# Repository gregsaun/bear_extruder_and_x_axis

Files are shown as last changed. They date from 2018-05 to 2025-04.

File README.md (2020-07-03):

# Bear Extruder And X Axis (BearExxa)

## Table of contents
  1. [Introduction](#introduction)
  1. [Features](#features)
  1. [Compatibility](#compatibility)
  1. [Printed parts](#printed-parts)
  1. [Print settings](#print-settings)
  1. [Bill of materials](#bill-of-materials)
  1. [Manual](#manual)
  1. [Optional parts](#optional-parts)
  1. [Community](#community)
  1. [Images](#images)
  1. [Source](#source)
  1. [Support my work](#support-my-work)
  1. [Thank you](#thank-you)
  1. [License](#license)
  1. [Credit and inspiration](#credit-and-inspiration)

## Introduction

The BearExxa (Bear extruder and X axis) is an alternative extruder and X axis for Prusa i3 printer and is designed to improve print quality, reliability and ease of maintenance. It is following the [Bear Upgrade project](https://github.com/gregsaun/prusa_i3_bear_upgrade) but also compatible with Original Prusa's MK2(S) and MK3(S) frames.

The Bear X axis also supports alternative extruders such as [Bondtech Prusa Upgrade](./optional_parts/bondtech_x_carriage/README.md), [E3D Hemera](./optional_parts/bear_hemera/README.md) and [vertigo235's extruders](https://www.thingiverse.com/vertigo235/designs).

All parts are available under the GPLv3 open source license. You can download STL, CAD files (Autodesk Fusion 360) or STEP files. Feel free to fork and share!

:warning: The Bear X axis is **NOT** compatible with stock Prusa extruder!

## Features

### Bear X axis (and X carriage)

  * Simple and precise belt tensioning system
  * Stiffer X axis design to reduce ringing
  * Easier Z bearings installation thanks to clamping system
  * Optimized belt path for smoother movements
  * Easy access to belt and extruder cables
  * Improved X axis bearing alignment
  * Kinematic constraint to self-center the X stepper
  * Optional: Support for alternative extruders
  * Optional: Compatible with E3D Gates idlers

### Bear extruder

  * Better heat management to reduce inconsistency, clogs and heatcreap (also check these [recommended hotend fans](optional_parts/hotend_fan/README.md))
  * Stiffer extruder thanks to a uni-body structure
  * Easier installation and removal of E3D v6 hotend
  * Efficient part cooling
  * Self-centering of extruder motor and Bondtech gears
  * Reduced risk of [extruder blob](https://www.prusa3d.com/extruder-blob/)
  * Reliable filament sensor (based on MK2.5S/MK3S sensor)
  * Perfectly aligned filament path
  * Reduced extruder and Bondtech gear vibrations
  * Reduced wear and noise of print fan thanks to a vertical assembly
  * Optional: Compatible with MMU2S thanks to the work of [vertigo235](https://www.thingiverse.com/vertigo235/designs)

### Alternative extruders (optional)

The Bear X axis is also compatible with several alternative extruders. See [optional parts](#optional-parts) to get all the information and files for those alternative extruders.

  * [E3D Hemera](optional_parts/bear_hemera/README.md)
  * [Bondtech Prusa Upgrade extruder](optional_parts/bondtech_x_carriage/README.md)
  * [Bear extruder for MMU2S by vertigo235](https://www.thingiverse.com/thing:3472911)
  * [Gear box for Bear extruder by vertigo235](https://www.thingiverse.com/thing:3714978)
  * [Bear Extruder BLTouch Mount by vertigo235](https://www.thingiverse.com/thing:3251530)

## Compatibility

Due to a different belt path, the Bear X axis and extruders are matched to each other __and cannot be used separately__. As a unit, they are compatible with both Original Prusa frames and Bear Upgrade frames.

  * The Bear extruder version supports the new IR filament sensor introduced with the latest Original Prusa MK2.5S/MK3S extruder.
  * The Bear extruder version is compatible with original Prusa firmware for daily use. However, (XY)Z calibration and selftest require a dedicated firmware for these steps only.
  * MK2.5 (non-S) and MK3 (non-S) are compatible with this Bear extruder version with the exception of the filament sensor.

In an effort to lengthen the Z axis, the original Prusa MK2.5S/MK3S hotend was raised by [about 6mm](doc/prusa_mk3_mk3s_size_diff_01.jpg). This placement increases the ambient temperature around heatbreak and heatblock which could lead to print quality and reliability issues. We have decided to not lengthen the Z axis in order to provide best printing experience. Because of this difference with the original Prusa extruder, we provide a customized firmware to pass Selftest and (XY)Z Calibration. Except for these steps, the original Prusa firmware is completely compatible with our extruder.

The firmware is available here: https://github.com/bear-lab-3d/Prusa-Firmware/releases/

## Printed parts

Download links for the Bear extruder and X axis (BearExxa) :
* BearExxa MK2.5S : [bear_extruder_x_axis_mk2.5s.zip](printed_parts/bear_extruder_x_axis_mk2.5s.zip?raw=true)
* BearExxa MK3S : [bear_extruder_x_axis_mk3s.zip](printed_parts/bear_extruder_x_axis_mk3s.zip?raw=true)
* Sources : [bear_extruder_x_axis_source.zip](source/bear_extruder_x_axis_source.zip?raw=true)

You can also download them via Thingiverse: [thingiverse.com/thing:4362586](https://www.thingiverse.com/thing:4362586)

If you are looking for alternative extruders printed parts, please check the section [Optional parts](#optional-parts) below.

## Print Settings

The parts have been designed and tested with the parameters below and it is important to follow them to avoid issues like part cracking, bad bridging, not enough stiffness or wrong tolerances.

[Read the print settings here](manual/print_settings.md).

## Bill of materials

[Read the BOM here](manual/bom.md).

## Manual

The manual contains bill of materials (BOM), print settings and assembly instructions.

[Read the manual on guides.bear-lab.com :book:](https://guides.bear-lab.com/c/95jghwzvw9l46s3g)

## Optional parts

Here is a list of optional parts designed for the Bear extruder and X axis (BearExxa).

| Description | Link |
|---|---|
| E3D Hemera mount (BearMera) | [bear_hemera](optional_parts/bear_hemera/README.md) |
| X carriage for Bondtech extruder | [bondtech_x_carriage](optional_parts/bondtech_x_carriage/README.md) |
| Hotend fan (Sunon / Delta) | [hotend_fan](optional_parts/hotend_fan/README.md) |
| X end tensioner for E3D idlers | [x_end_idler_tensioner_e3d](optional_parts/x_end_idler_tensioner_e3d/README.md) |
| Reverse bowden adapters | [reverse_bowden](optional_parts/reverse_bowden/README.md) |
| X carriage back for larger filament sensor cable |[x_carriage_back_larger_cable](optional_parts/x_carriage_back_larger_cable/README.md) |

You can also find optional parts made by the community at [guides.bear-lab.com/Wiki/community_optional_parts](https://guides.bear-lab.com/Wiki/community_optional_parts).

## Community

Here are the places were the Bear project is the most active. Do not hesitate to ask if you have a question :

* Facebook group : [facebook.com/groups/PrusaBearUpgrade](https://www.facebook.com/groups/PrusaBearUpgrade)
* Discord server of "The 602 Wasteland" community : [discordapp.com/invite/hYUjSnW](https://discordapp.com/invite/hYUjSnW)
* Twitter : [@gregoiresaunier](https://twitter.com/gregoiresaunier)
* GitHub : [github.com/gregsaun](https://github.com/gregsaun)

## Images

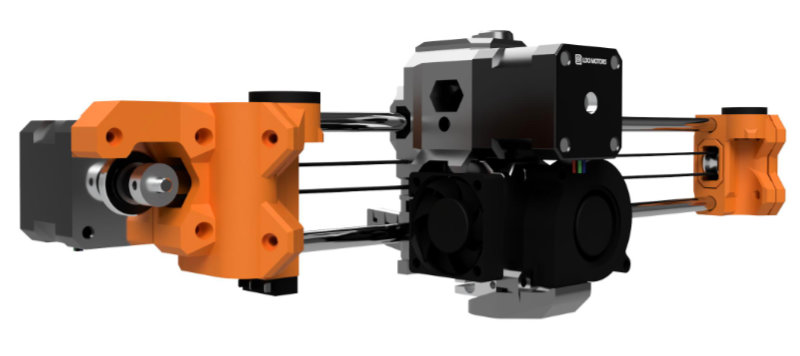
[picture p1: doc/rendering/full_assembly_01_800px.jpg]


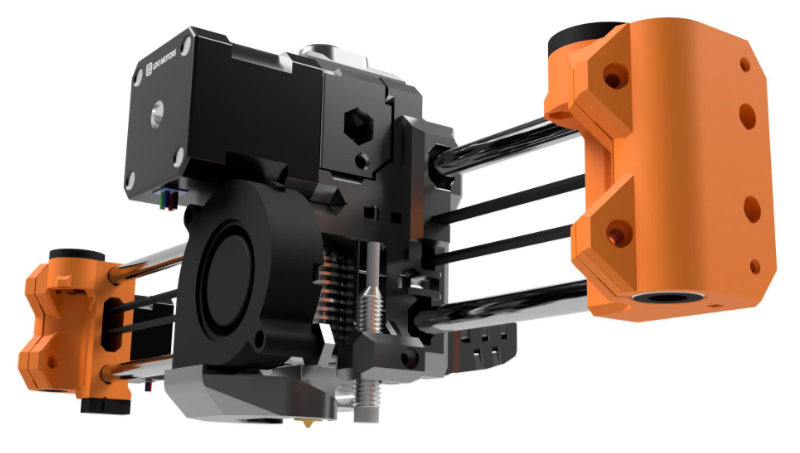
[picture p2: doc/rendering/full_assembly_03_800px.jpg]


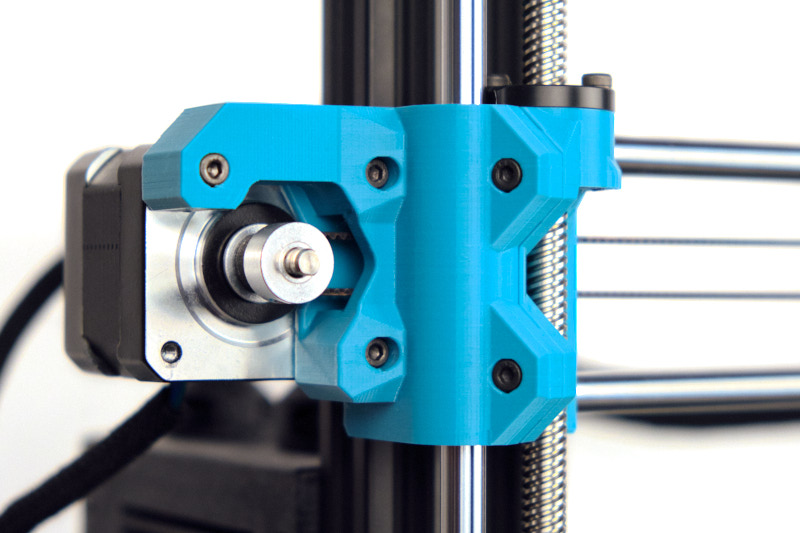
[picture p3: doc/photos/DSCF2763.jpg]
Bear X end motor


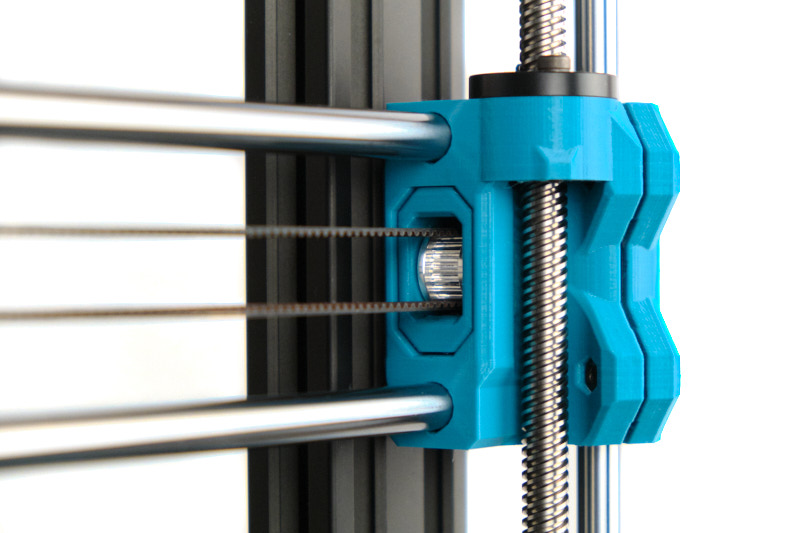
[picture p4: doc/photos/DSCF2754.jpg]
Bear X end idler


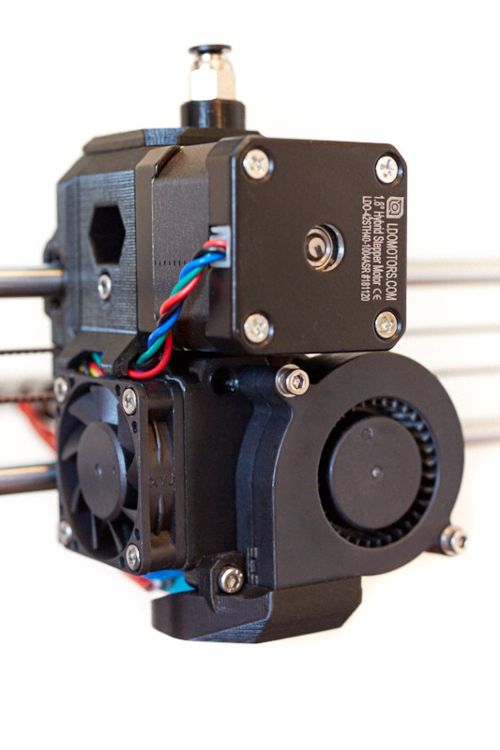
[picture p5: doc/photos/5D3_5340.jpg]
Bear extruder


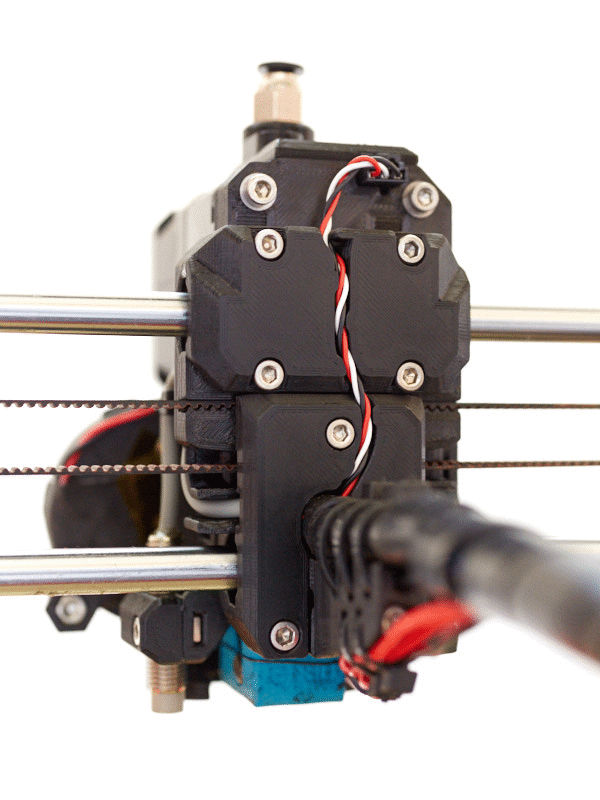
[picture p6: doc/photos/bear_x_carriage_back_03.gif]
Bear extruder X carriage back


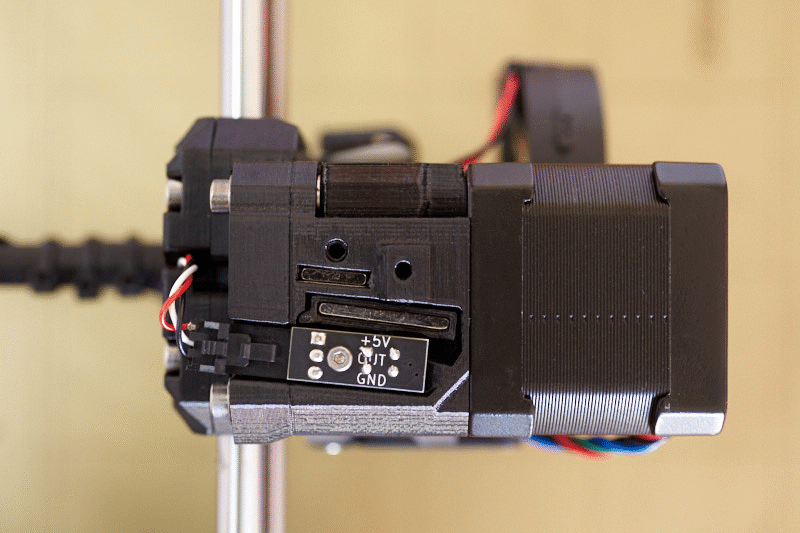
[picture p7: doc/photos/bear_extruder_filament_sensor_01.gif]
Bear extruder filament sensor


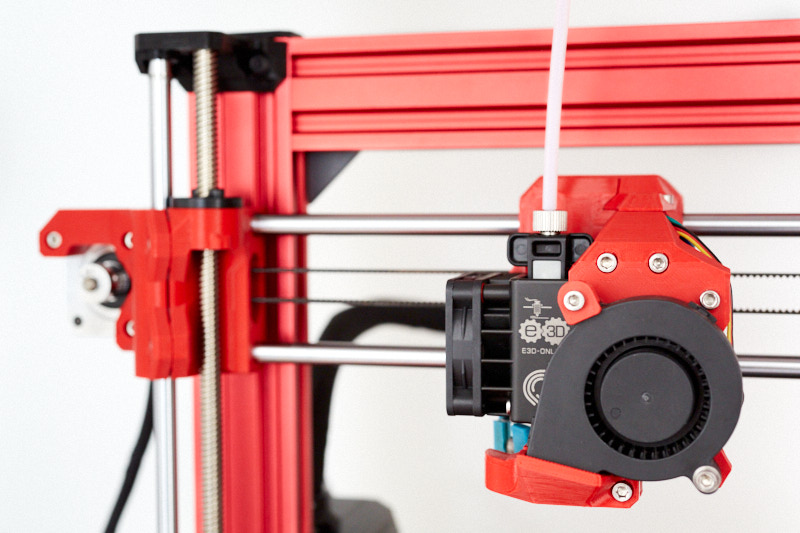
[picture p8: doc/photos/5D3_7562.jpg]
Bear E3D Hemera


> Pictures from Flobler and Grégoire Saunier

## Source

All source files in Fusion 360 and STEP format can be [download here](source/bear_extruder_x_axis_source.zip?raw=true).

## Support my work

The Bear project is only possible thanks its supporters, you can participate via
<br/><br/>
become a patron (https://www.patreon.com/gregsaun)<br/>[patreon.com/gregsaun](https://www.patreon.com/gregsaun)
<br/><br/>
paypal.me (https://www.paypal.me/gregsaun)<br/>[paypal.me/gregsaun](https://www.paypal.me/gregsaun)
<br/><br/>
 You can also send me a tip via [Thingiverse](https://www.thingiverse.com/pekcitron/about) if you prefer.

Massive thank you in advance :heart:

## Thank you

First of all, massive thank you to [Adrian Bowyer](https://github.com/AdrianBowyer/) for having invented [RepRap](http://reprapltd.com).

Thank you to all [my Patreon's](https://guides.bear-lab.com/Wiki/Bear_Supporters)

Thank you to David Ogles, Flobler, Jason from LDO Motors, Matthew Humphrey, Nathan Denkin, Orlando from All3DMakers, Saiz, Sleene, Termlimit, Vertigo235 for helping me in developing the Bear project.

Thank you to all that have sent me a tip on Thingiverse and PayPal.

Thank you to everybody from Facebook group and The 602 Wasteland community.

Thank you for having purchased a kit from an official distributor.

Thank you to all official distributors for taking care of the kits and customers.

Thank you Jason from LDO Motors for the quality manufacturing and relationship.

Thank you Openbuilds for your hardware, community and state of mind.

Thank you for making the community alive with all your comments, issues, pull requests, optional parts, make, pictures, etc.

## License

This repository and all its files are licensed under the GPLv3 license. Here is a quick summary; for more details please check the LICENSE file.

What you __can__ do:
  * Modify
  * Distribute
  * Private, commercial and patent use

What you __must__ do:
  * Include copyright notice
  * Include a copy of the license
  * Share source files
  * Use the same license (GPLv3)
  * Document changes applied

## Credit and inspiration

* RepRap : https://reprap.org
* Prusa : http://www.prusa3d.com
* Vecko Kojchevski for the help on some details of the X end clamps, X carriage and PTFE cutter : https://www.thingiverse.com/vekoj/designs
* Arnaud Rousseau for "his X-Ends clamped MK3 (Zaribo)" : https://www.thingiverse.com/thing:2964026
* Prusa i3 Solidworks parts from jzkmath : https://github.com/jzkmath/Original-Prusa-i3
* Prusa MK2/S X-Carriage Adjustable Tensioner by Jon Madden : https://www.thingiverse.com/thing:2770019
* Jan Imrich from [Kurzy Kocour](https://www.facebook.com/KurzyKocour/) maker space for all his hard work on inconsistency issue
* The 602 Wasteland Discord community for their precious knowledge and advice
* [RH_Dreambox](https://www.thingiverse.com/RH_Dreambox/about) and [Robrps](https://www.thingiverse.com/robrps/designs) for his nozzle fan duct designs
* Joel from [Bondtech](https://www.bondtech.se/en/product/prusa-i3-mk2-5-mk3-extruder-upgrade/) for having pushed me to pursue the filament sensor idea

Massive thanks to these projects, without them this project cannot exist!

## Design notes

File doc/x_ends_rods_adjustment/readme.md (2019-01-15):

This explains how to adjust the rod tensioning screws on the x end idler. It also discusses the limits of Prusa’s X axis design.

Those screws were present on the MK2s but were removed on the MK3, perhaps making it simpler for the user and to reduce cost. However, while not obvious, those screws can play a critical role.

Due to manufacturing tolerances, user assembly and somewhat flexible printed parts (especially PETG), the X axis length between the Z axis smooth rods will differ between assemblies, for both Bear and original Prusa printers.

This first picture shows an exaggerated view of what is happening when tensioning the belt with too short X smooth rods.

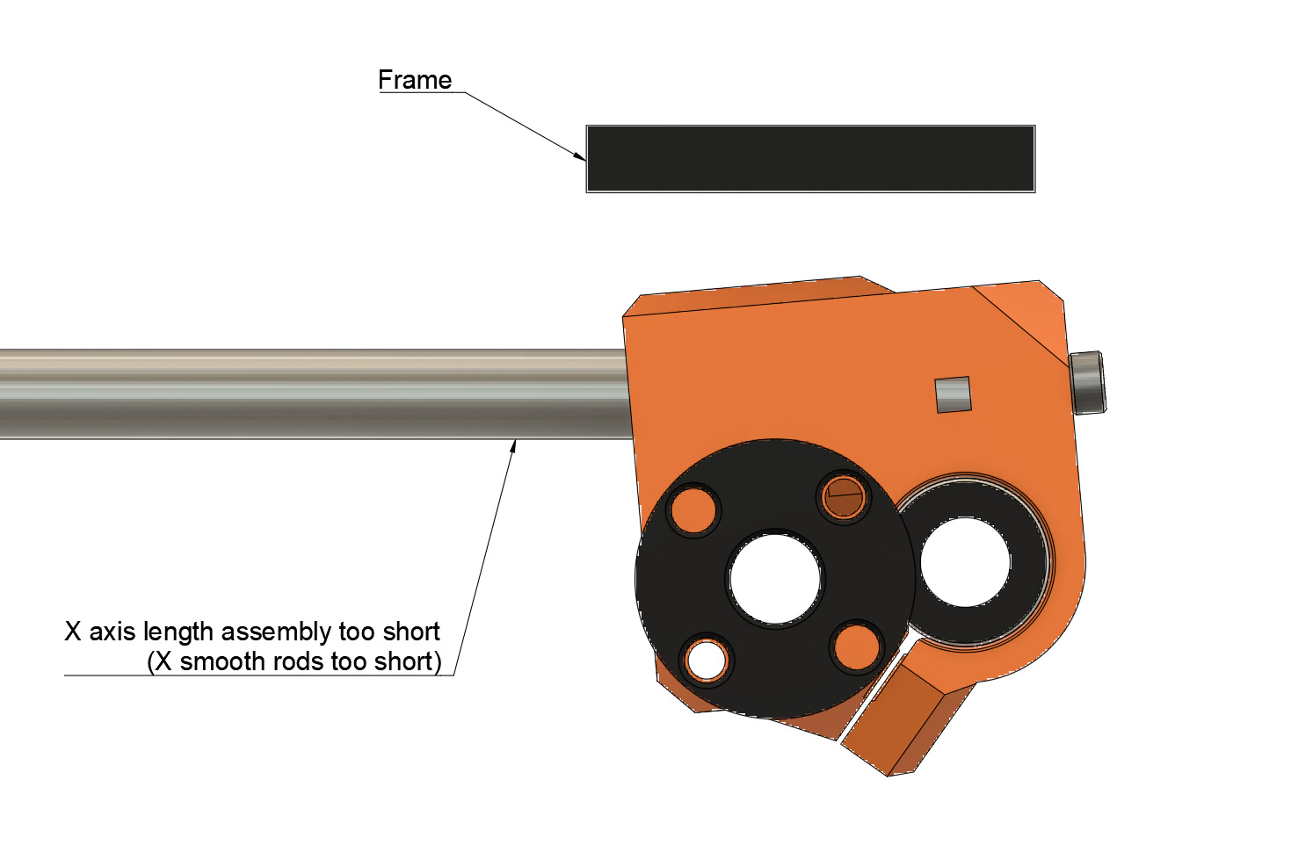
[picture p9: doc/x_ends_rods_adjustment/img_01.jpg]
X axis length too short


This second picture shows when the X smooth rods are too long.

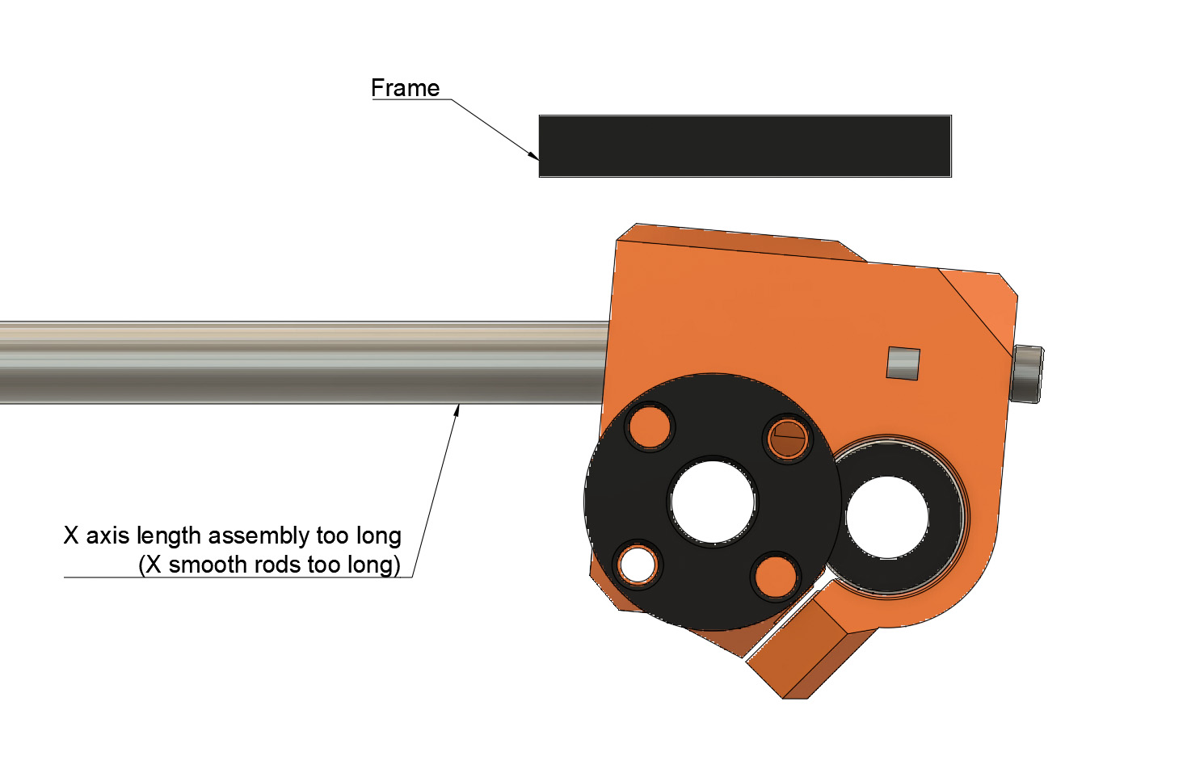
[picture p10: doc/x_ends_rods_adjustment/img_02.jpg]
X axis length too long


These rotations of the X end idler around the Z axis result because the ends X smooth rods are not aligned with the Z axis generating a torque that twists the X end idler. The rod tensioning screws can be used to reduce that torque. 

The third picute shows when the tensioning screw are correctly set, the X end idler is parallel to the frame

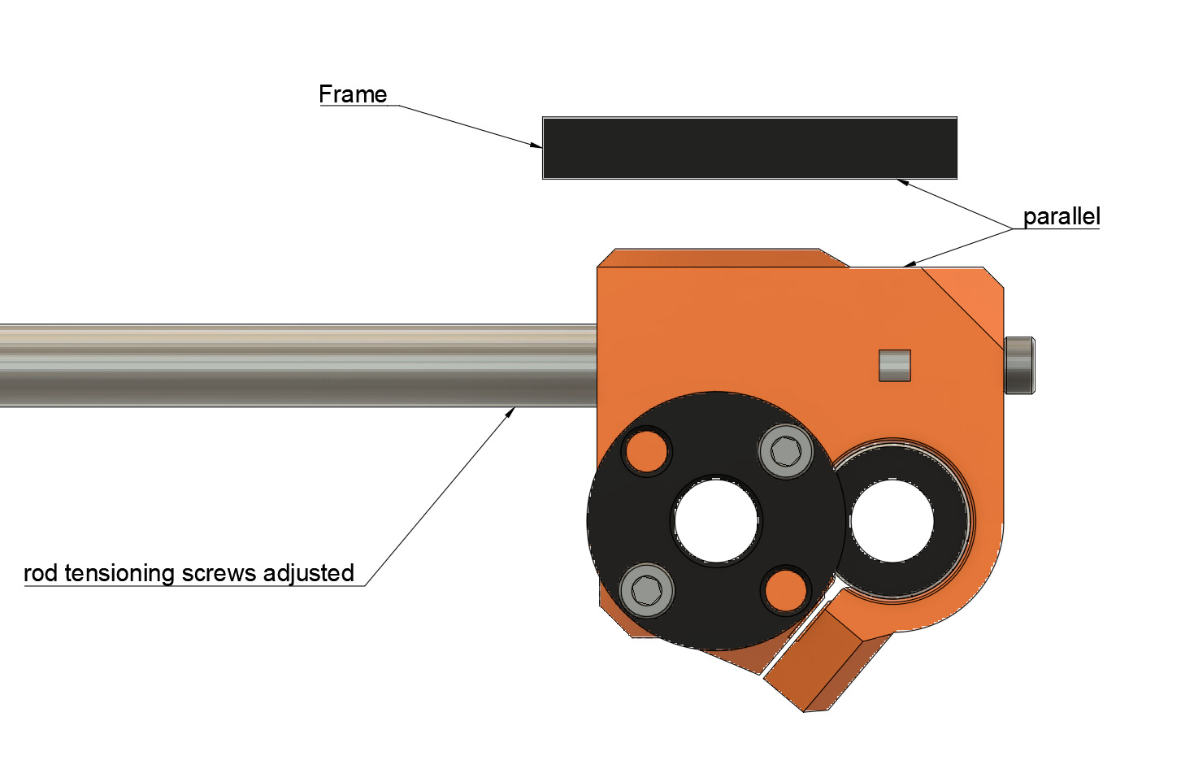
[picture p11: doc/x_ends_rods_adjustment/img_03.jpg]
X axis length good


A good way to check if the X end idler is parallel is to use a machinist square like it this picture.

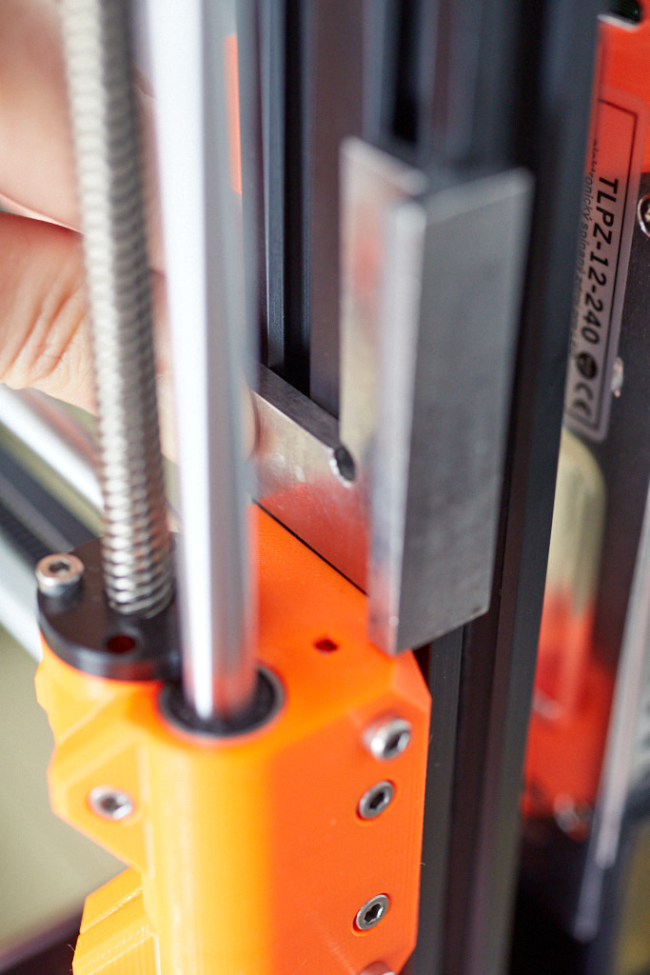
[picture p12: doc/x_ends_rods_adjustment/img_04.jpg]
X axis check


Usually, the pairs of smooth rods have the same length; in that case, both rod tensioning screw heads should stick out of the X end idler by the same distance that could be verified by a caliper.

However, with Prusa’s design, the X axis and Z axis interact. If the distance between the X end idler and the X motor is too large, the Z rods would be pushed apart, and you would see that the Z rods off-center in with respect to the Z tops. Similarly, if the distance between the X end idler and the X motor is too small, the Z rods would be pulled together. The trapezoidal lead screw nut has some play and can influence this. The screws securing both trapezoidal nuts should be loosened while the X axis is being adjusted. All these interactions makes a perfect assembly almost impossible to achieve.

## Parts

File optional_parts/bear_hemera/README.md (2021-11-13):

# Bear X axis and Extruder

## BearMera for E3D Hemera extruder

### Table of contents
  1. [Introduction](#introduction)
  1. [Compatibility](#compatibility)
  1. [Bill Of materials](#bill-of-materials)
  1. [Printed parts](#printed-parts)
  1. [Print settings](#print-settings)
  1. [Assembly guide](#assembly-guide)
  1. [Optional parts](#optional-parts)
  1. [Source](#source)
  1. [Thank you](#thank-you)
  1. [Credit and inspiration](#credit-and-inspiration)

### Introduction

This page contains all the files and information to use the Bear X axis with the original [E3D Hemera](https://e3d-online.com/e3d-hemera).

The Hemera needs a dedicated mount to be used with the Bear X axis. All hardware and printed parts needed are available in the [Bill of Materials](#bill-of-materials) section below.

Note: The BearMera reduces a little the print surface to 205x240mm (compared to 210x250mm for Original Prusa).

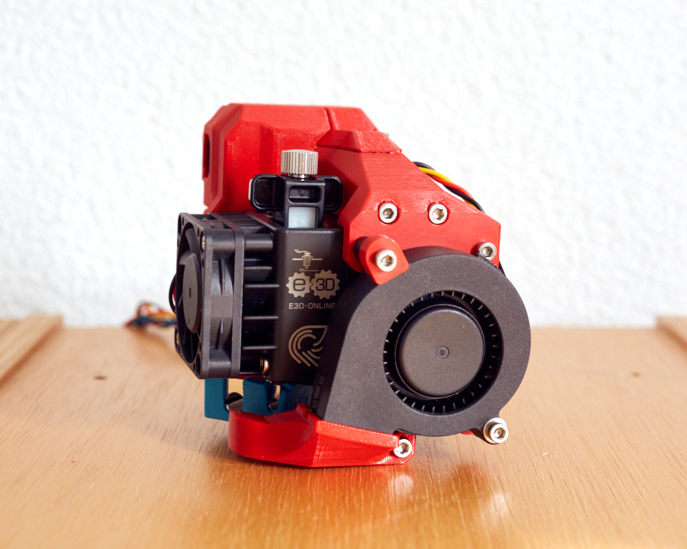
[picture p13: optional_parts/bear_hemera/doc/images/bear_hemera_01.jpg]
Bear Hemera body


### Compatibility

The BearMera has a smaller print surface compared to the Original Prusa, Bear and Bondtech extruders: 205x240mm for BearMera, 210x250mm for Bear extruder.

The BearMera is compatible with Original Prusa as well as Bear frame. You must use the Bear X axis in both cases.

This BearMera is only compatible with the Bear X axis.

This BearMera is **NOT** compatible with the original Prusa X axis.

You will need to replace **all** printed parts if you are already using the Bear X axis (with another extruder) of version **equal or smaller than 0.7.0-beta**.

### Bill Of materials

#### Hardware BOM for Original Prusa printers

This is the list of extra material you will need from original Prusa extruder and X axis.

| Part | Quantity<br>(pce) | Detail | Example Link |
|---|:---:|---|---|
| E3D Hemera Direct Kit | 1 | 24V for MK3(S)(S+)<br>12V for MK2(S) and MK2.5(S)(S+) | [E3D-Online store](https://e3d-online.com/e3d-hemera) |
| Hotend fan | 1 | Stock Hemera fan<br/>or higher specifications (yet unknown) | |
| M3x8mm socket head screw (ISO 4762) | 3 | Check your Hemera package | [McMaster-Carr](https://www.mcmaster.com/90751a111) | |
| M3x10mm socket head screw (ISO 4762) | 12 | | [McMaster-Carr](https://www.mcmaster.com/#91292a113/=1coixe5) | |
| M3x18mm socket head screw (ISO 4762) | 16 | | [McMaster-Carr](https://www.mcmaster.com/#91292a029/=1coixwt) | |
| M3x25mm socket head screw (ISO 4762) | 2  | | [McMaster-Carr](https://www.mcmaster.com/#91292a020/=1cok8ux) | |
| M3x40mm socket head screw (ISO 4762) | 3  | | [McMaster-Carr](https://www.mcmaster.com/#91292a024/=1coj8pe) | |
| M2x12mm socket head screw (ISO 4762) | 2  | :warning: MK2(S) or MK2.5(S) only | [McMaster-Carr](https://www.mcmaster.com/#91292a834/=1cok8m8) |
| M3 Hex nylock nuts (DIN 985) | 3  | | |
| M3 Hex nuts (DIN 934) | 15 | | |
| M3 Square nuts (DIN 562) | 6  | 1.8mm thick and 5.5mm wide | |
| M3 Steel washer (DIN 125), 0.5mm thick | 1  | | |
| Zip ties 2.5x100mm | 5  | | |
| Dowel pin<br/>diameter: 3mm, length: 15mm to 15.8mm | 1 | Must fit the 2GT idler bearing.<br/>:pushpin: Cut a M3 screw if you can't find one |

#### Additional BOM for scratch build

| Part | Quantity<br>(pce) | Detail | Example Link |
|---|:---:|---|---|
| Nema 17 stepper for X axis<br/>LDO 42STH38-1004A100CM | 1 | [Datasheet](https://github.com/gregsaun/bear_extruder_and_x_axis/tree/master/doc/datasheets/LDO-42STH38-1004A100CM-RevA-for-3D.pdf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) | [Prusa](https://shop.prusa3d.com/en/mk3mk3s/388-x-axis-stepper-motor.html) |
| Nema 17 stepper for Z axis<br/>integrated Lead screw Tr8x8 (P2x4) and nut<br/>LDO-42STH34-1004L321E100CM | 2 | [Datasheet](https://github.com/gregsaun/bear_extruder_and_x_axis/tree/master/doc/datasheets/LDO-42STH34-1004L321E100CM-RevA-for-3D.pdf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) | [Prusa](https://shop.prusa3d.com/en/spare-parts/386-stepper-motor-z-axis-right.html) |
| Nozzle Fan | 1 | Minimal specifications:<br/>- CFM: 3.8<br/>- Static Pressure: 11.3 mmH2O<br/>- Bearing type: ball bearing | [Prusa](https://shop.prusa3d.com/en/spare-parts/201-print-fan.html) |
| Inductive Sensor | 1 | Diameter of 8mm, length around 35mm | | [Prusa](https://shop.prusa3d.com/en/spare-parts/200-pinda-probe-v2.html) |
| Filament sensor<br/>with magnets, steel ball and cables | 1 | 1x IR Sensor: [GitHub Prusa](https://github.com/prusa3d/MKxS-IR-sensor)<br/>1x Steel ball 7mm diameter<br/>1x Magnet 20x6x2<br/>1x Magnet 10x6x2<br/> | [Prusa](https://shop.prusa3d.com/en/upgrades/898-original-prusa-i3-mk3-to-mk3s-upgrade-kit.html#) |
| 2GT 16T pulley | 1 | 3mm bore<br/> | [E3D-Online store](https://e3d-online.com/gates-powergrip-pulley-16-tooth-6mm) |
| 2GT 20T idler | 1 | 3mm bore<br/>smooth or toothed<br/>Check this [optional part for E3D idler](https://github.com/gregsaun/bear_extruder_and_x_axis/tree/master/optional_parts/x_end_idler_tensioner_e3d) | |
| Smooth rods | 2 | 8mm diameter H6<br/>370mm long | [Prusa](https://shop.prusa3d.com/en/mk3mk3s/589-smooth-rod-8x370-x-axis-1-piece.html) |
| LM8UU bearings | 3 | [Prusa](https://shop.prusa3d.com/en/mk3mk3s/140-linear-bearing-lm8uu.html) |
| Gates LL-2GT RF belt | 1 | 6mm width<br/>880mm long | [E3D-Online store](https://e3d-online.com/gates-powergripr-gt2-belt-6mm-x-100mm) |
| Nylon cable<br/>2.85-3.00mm diameter<br/>500mm long | 1 | You can use 2.85mm sample or cleaning filaments | |

### Printed parts

Download links for the BearMera and X axis:
  * BearMera and X axis for MK2(S) and MK2.5(S): [bearmera_mk2_mk2s_mk2.5_mk2.5s.zip](printed_parts/bearmera_mk2_mk2s_mk2.5_mk2.5s.zip?raw=true)
  * BearMera and X axis for MK3(S) and MK3(S): [bearmera_mk3_mk3s.zip](printed_parts/bearmera_mk3_mk3s.zip?raw=true)

### Print settings

:warning: Warning: The parts have been designed and tested with the parameters below and it is important to follow them to avoid issues like part cracking, bad bridging, not enough stiffness or wrong tolerances. Be sure to have a well calibrated machine and extruder. Check our guide here for [calibrating extrusion multiplier](https://guides.bear-lab.com/Guide/Extrusion+multiplier+and+filament+diameter/8?lang=en)

  * Slicer : PrusaSlicer recommended
  * Infill type : Gyroid recommended
  * Support : No
  * Brim : No
  * Detect thin walls : No
  * Perimeters width (internal and external) : 0.45mm

| Part | Quantity | Layer Height | Infill | Perimeters | Top/Bottom Layers | Filament Type |
|:----|:----:|:----:|:----:|:----:|:----:|:----:|
| body_back | 1 | 0.20mm | 20% | 4 | 5 | PETG |
| body_front<sup>1</sup>  | 1 | 0.20mm | 20% | 4 | 5 | PETG |
| cable_cover | 1 | 0.20mm | 20% | 4 | 5 | PETG |
| nozzle_fan_duct | 1 | 0.20mm | 20% | 3 | 5 | Read note<sup>2</sup> below |
| nozzle_fan_spacer | 1 | 0.20mm | 20% | 4 | 5 | PETG |
| pinda_mount | 1 | 0.20mm | 20% | 4 | 5 | PETG |
| ptfe_collet_clip | 1 | 0.20mm | 20% | 3 | 5 | PETG |
| y_axis_end_stop | 1 | 0.20mm | 20% | 3 | 5 | PETG |
| x_carriage | 1 | 0.20mm | 20% | 4 | 5 | PETG |
| x_carriage_back | 1 | 0.20mm | 20% | 3 | 5 | PETG |
| x_end_idler | 1 | 0.20mm | 20% | 4 | 5 | PETG |
| x_end_idler_tensioner | 1 | 0.20mm | 20% | 4 | 5 | PETG |
| x_end_motor | 1 | 0.20mm | 20% | 4 | 5 | PETG |
| cable_guide_back_a | 1 | 0.20mm | 20% | 4 | 5 | PETG |
| cable_guide_back_b | 1 | 0.20mm | 20% | 4 | 5 | PETG |

Note<sup>1</sup>: If you intend to use the E3D Volcano hotend with BearMera, this STL should be replaced with the [modified volcano body_front](optional_parts/e3d_volcano/) listed below among official [Optional parts](#optional-parts)

Note<sup>2</sup>: The nozzle_fan_duct needs to be printed with a heat resistant filament like ABS, Extrudr GreenTec Pro, annealed HTPLA, PC and probably much more. Don't forget to compensate for shrinkage accordingly to the filament type you are using.

You can find more details about recommended filaments in on our [FAQ](https://guides.bear-lab.com/Wiki/Bear_FAQ).

### Assembly guide

The assembly guide is available on [guides.bear-lab.com](https://guides.bear-lab.com/c/r63d85yfkvrohzf1).

### Optional parts

Here is a list official optional parts for your BearMera.

| Name | Description | Link |
|---|---|---|
| E3D Volcano | A body_front to support E3D Volcano | [optional_parts/e3d_volcano](optional_parts/e3d_volcano/) |
| Fan washer | Allow a stronger tightening of the E3D fan by avoiding it to twist | [optional_parts/fan_washer](optional_parts/fan_washer/) |

### Source

All source files in Fusion 360 and STEP format can be [download here](source/bearmera_source.zip?raw=true).

### Thank you

Thank you to [E3D-Online](https://e3d-online.com) for their warm encouragement and for having sponsor this development with a free Hemera.

### Credit and inspiration

  * E3D Hemera Prusa i3 MK2(S) upgrade: https://e3d-online.dozuki.com/Guide/Hemera+Prusa+i3+MK2-2s+upgrade/138?lang=en

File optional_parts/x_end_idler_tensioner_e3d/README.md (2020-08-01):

# Bear X axis and Extruder (BearExxa)

## X-End Idler Tensioner for E3D toothed idler

### Introduction

This is a X end idler tensioner compatible with E3D toothed idler.

### Bill of materials

This is the list of extra material you will need from original Prusa extruder

| Part | Quantity<br>(pce) | Detail |
|---|:---:|---|
| Bear X axis | 1 | From version 0.6.0-a and greater |
| E3D Gates 2GT Toothed Idler<br/>6mm Belt, 20 Tooth, 5mm ID | 1 | https://e3d-online.com/products/gates-powergrip%C2%AE-2gt-idlers |
| Dowel pin<br/>diameter: 4.90-4.95mm<br/>length: 15mm-15.8mm | 1 | Must fit the 2GT idler bearing.<br/>:pushpin: Cut a M5 screw if you can't find one |
| M3 Hex nylock nuts (DIN 985) | 2 | Same as original Bear X end idler tensioner |

### Printed parts

Use this link to download the STL: [x_end_idler_tensioner_e3d.stl](printed_parts/x_end_idler_tensioner_e3d.stl?raw=true)

### Print settings

:warning: Warning: The parts have been designed and tested with the parameters below and it is important to follow them to avoid issues like part cracking, bad bridging, not enough stiffness or wrong tolerances. Be sure to have a well calibrated machine and extruder. Check our guide here for [calibrating extrusion multiplier](https://guides.bear-lab.com/Guide/Extrusion+multiplier+and+filament+diameter/8?lang=en)

  * Slicer : PrusaSlicer recommended
  * Infill type : Gyroid recommended
  * Support : No
  * Brim : No
  * Detect thin walls : No
  * Perimeters width (internal and external) : 0.45mm

| Layer Height | Infill | Perimeters | Top/Bottom Layers |
|:----:|:----:|:----:|:----:|
| 0.20mm | 20% | 4 | 5 |

### Credits

Thanks to Matthew Humphrey for having created the first version of this idler.
https://www.thingiverse.com/thing:3308226

What is changing from Matthew's design:
  * Improves shape and tolerances around the E3D idler
  * Derivation from the original design (using F360 derive feature)

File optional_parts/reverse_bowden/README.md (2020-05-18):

# Bear X axis and Extruder (BearExxa)

## Reverse Bowden

### Introduction

Reverse bowden has the advantage to reduce vibration and tension from the spool holder. It is also useful to guide the filament if the spool holder is not on top of the frame.

The filament sensor cover can be used alone for MMU2.

The vslot mount is available in two versions: angled or normal.

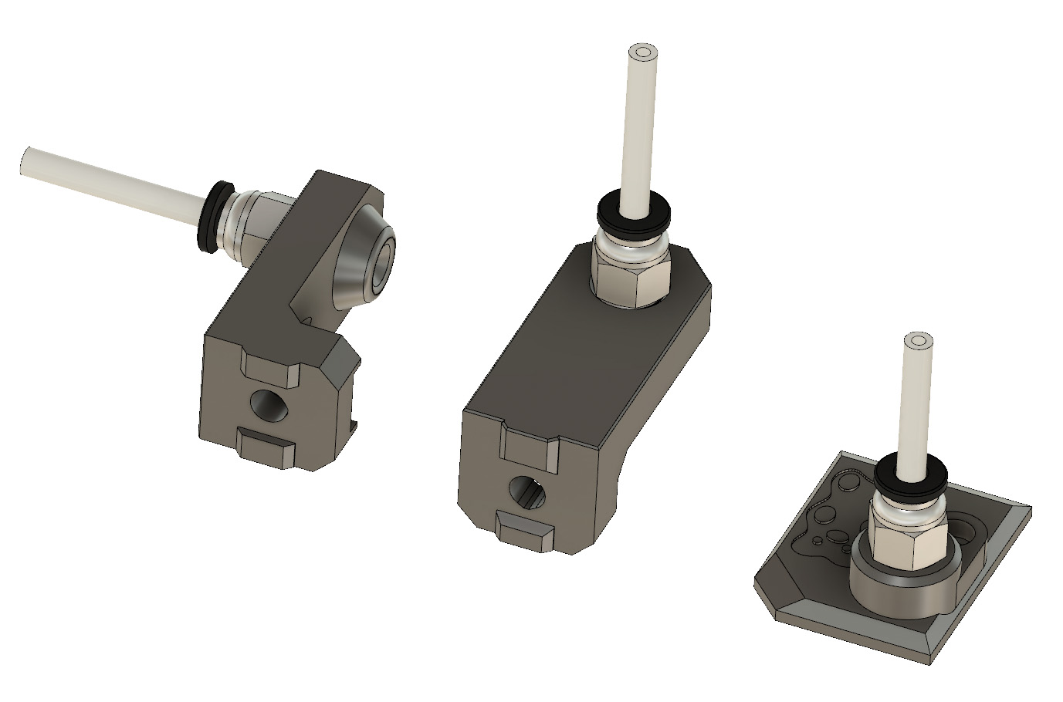
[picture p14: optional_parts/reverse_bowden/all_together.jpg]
Reverse bowden family


### Bill of Materials

| Part | Number<br>(pce) | Detail |
|---|:---:|---|
| Bear extruder and x axis| 1 | |
| PC4-M10 fitting | 2 | |
| PTFE tube | 1 | ID: 2mm, OD: 4mm |
| M5x10 screw | 1 | |

### Printed parts

Use those links to download the STL files:
  * [fs_cover_pc4-m10_mk25s_mk3s.stl](printed_parts/fs_cover_pc4-m10_mk25s_mk3s.stl?raw=true)
  * [vslot_mount_pc4-m10.stl](printed_parts/vslot_mount_pc4-m10.stl?raw=true)
  * [vslot_mount_pc4-m10_angled.stl](printed_parts/vslot_mount_pc4-m10_angled.stl?raw=true)

### Printed Settings

:warning: Warning: The parts have been designed and tested with the parameters below and it is important to follow them to avoid issues like part cracking, bad bridging, not enough stiffness or wrong tolerances. Be sure to have a well calibrated machine and extruder. Check our guide here for [calibrating extrusion multiplier](https://guides.bear-lab.com/Guide/Extrusion+multiplier+and+filament+diameter/8?lang=en)

  * Slicer : PrusaSlicer recommended
  * Infill type : Gyroid recommended
  * Support : No
  * Brim : No
  * Detect thin walls : No
  * Perimeters width (internal and external) : 0.45mm

| Part | Quantity | Layer Height | Infill | Perimeters | Top/Bottom Layers |
|:----|:----:|:----:|:----:|:----:|:----:|
| filament_sensor_cover_pc4-m10 | 1 | 0.20mm | 20% | 3 | 5 |
| vslot_mount_pc4-m10 | 1 | 0.20mm | 20% | 3 | 5 |
| vslot_mount_pc4-m10_angled | 1 | 0.20mm | 20% | 3 | 5 |

### Assembly

1. You need to replace the filament sensor cover by the one included here
1. Attach the vslot mount of your choice to the frame
1. Add the two PC4-M10 fittings
1. Cut the PTFE at the correct length
1. Insert the PTFE tube inside both PC4-M10 (be sure that the PTFE is fully inserted inside the vslot mount)

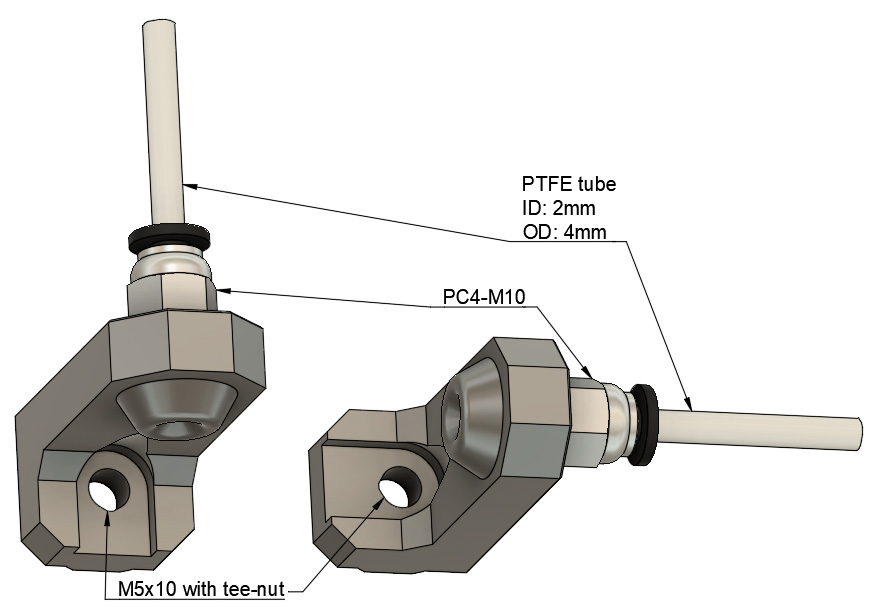
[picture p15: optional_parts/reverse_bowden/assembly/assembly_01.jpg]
Reverse bowden assembly


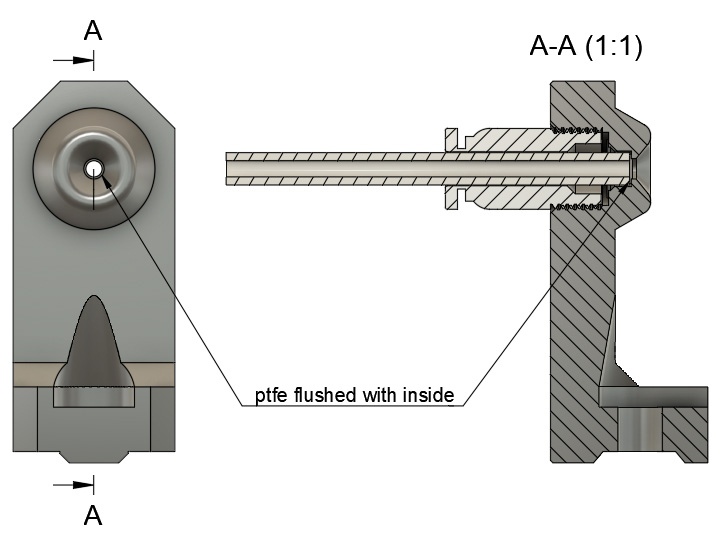
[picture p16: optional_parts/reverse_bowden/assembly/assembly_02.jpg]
Reverse bowden assembly


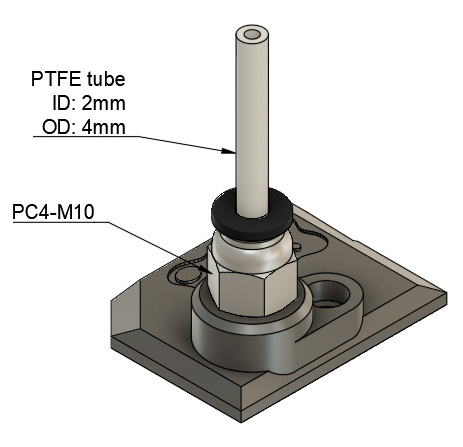
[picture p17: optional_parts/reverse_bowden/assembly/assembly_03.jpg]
Reverse bowden assembly


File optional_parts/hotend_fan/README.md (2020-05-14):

# Bear X Axis And Extruder (BearExxa)

## Upgrade of Noctua hotend fan

The Noctua fan used by Prusa is designed to provide airflow through a case, not force air through a heatsink. While the Bear extruder improves the Noctua efficiency, it is still not powerful enough. The Noctua lacks static pressure to force enough air through the fins of the heatsink and overcome the back pressure from the "reduction cone" matching to the E3D v6 heatsink.

On the table below, we can see that the original E3D v6 fan has 5.07 times more static pressure than the Noctua. In addition to the extra pressure, the E3D v6 fan does not need a "reduction cone" and is very close to the heatsink which is improving efficiency.

Less heatsink cooling allows the filament to melt higher in the heatbreak. This may affect the consistency of layer deposition and increase the risk of clogging. Increase of stringing might be another artefact of a higher heatsink temperature.

Fortunately, there are *almost* drop-in replacements for the Noctua from OEM3D, Sunon and Delta which are more powerful but more noisier (you cannot get more pressure with same noise level...) :
  * [OEM3D Hotend cooling fan](https://www.oem3d.com/products/oem3d-hotend-cooling-fan-for-mk3s-mk2-5s) (the most powerful)
  * Sunon MF40100V1-1000U-G99
  * Delta ASB0405HHA-AF00 (despite similar specs, a bit lower than Sunon)

Some distributors are selling the Sunon as a drop-in replacement with correct cable length and connector. However, you could source the fan on your own providing a cable and crimping a connector. The total cable length needs to be 700mm long. We recommend AWG 26 wire. The connector used on the RAMBo is Molex SL 70066 and contacts are Molex SL 70058.

:warning: You will need 4x M3x16mm button head or flat head screws to secure the fan while avoiding the Z lead screw.

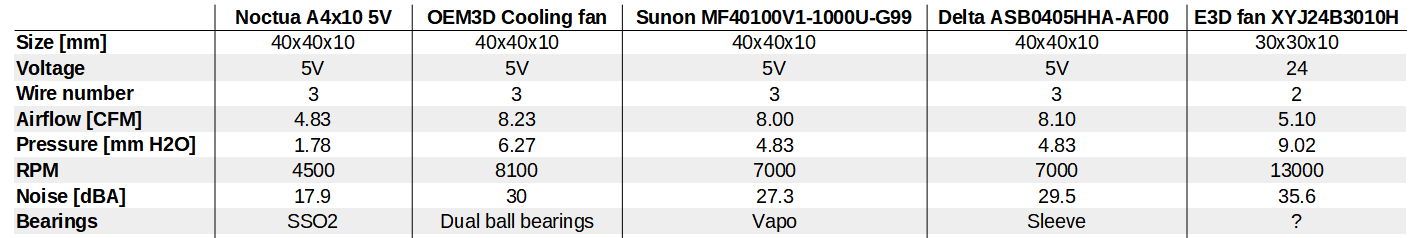
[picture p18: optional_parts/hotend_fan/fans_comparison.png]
Noctua vs Sunon


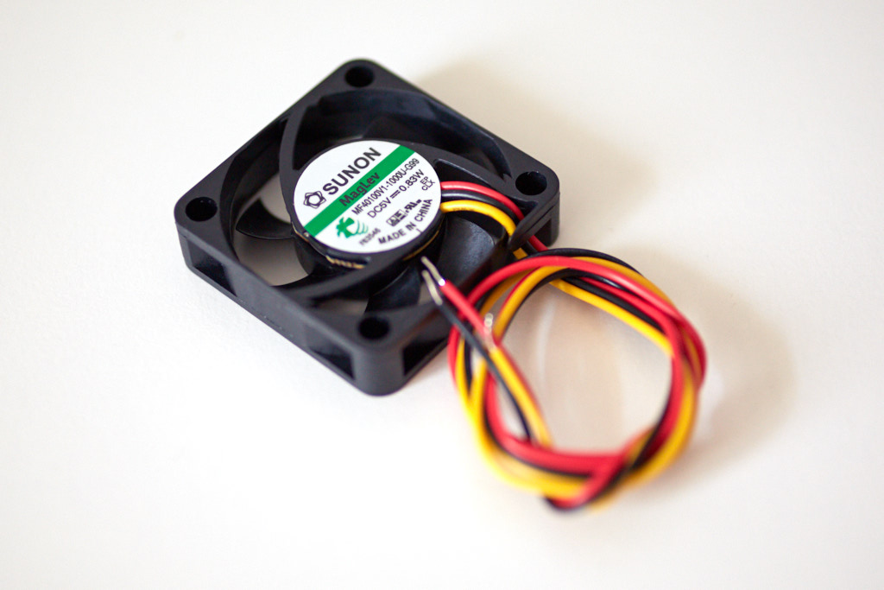
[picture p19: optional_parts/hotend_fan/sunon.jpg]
Sunon fan


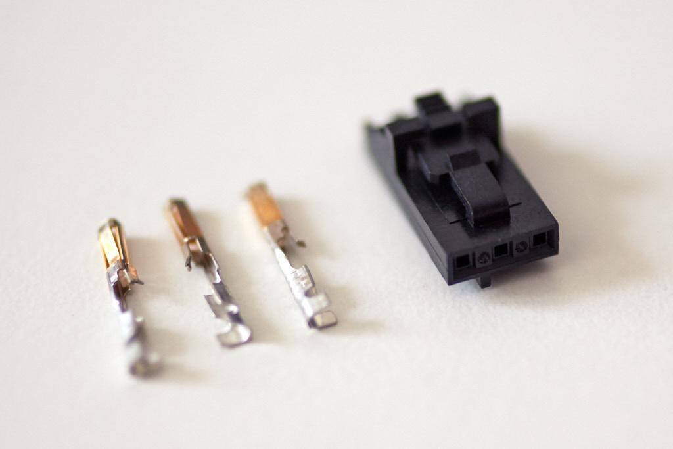
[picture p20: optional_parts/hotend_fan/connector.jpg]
Connector


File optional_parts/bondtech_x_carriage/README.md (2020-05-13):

# Bear X axis and Extruder

## Bondtech Prusa Upgrade Extruder

### Table of contents
  1. [Introduction](#introduction)
  1. [Compatibility](#compatibility)
  1. [Bill Of materials](#bill-of-materials)
  1. [Printed parts](#printed-parts)
  1. [Print settings](#print-settings)
  1. [Assembly guide](#assembly-guide)
  1. [Source](#source)

### Introduction

This page contains all the files and information to use the Bear X axis with the original [Bondtech Prusa Upgrade Extruder MK2(S), MK2.5(S), MK3(S), Mosquito MK2.5(S), Mosquito MK3(S)](https://www.bondtech.se/en/product-category/upgrade-kits/prusa/).

The original Bondtech Prusa Upgrade Extruder needs a dedicated Bear X carriage to be used with the Bear X axis.

:pushpin: Note that in order to be sure inconsistent extrusion is cured with this extruder we highly recommend to use one of [our recommended fans](../hotend_fan/README.md).

### Compatibility

Due to a different belt path, the Bear X carriage for Bondtech Prusa Upgrade extruder and Bear X axis (X ends) are matched to each other __and cannot be used separately__. As a unit, they are compatible with both Original Prusa frames and Bear Upgrade frames.

The Bear X carriage for Bondtech Prusa Upgrade is not compatible with Original Prusa X axis (X ends).

If you are already using the Bear X ends with another extruder, you only need to add this Bear X carriage for Bondtech Prusa Upgrade.

Note that the Bondtech Prusa Upgrade extruder needs a custom firmware, independently of the X axis used.

### Bill of materials

This is the list of extra material you will need from original Prusa extruder

| Part | Quantity<br>(pce) | Detail |
|---|:---:|---|
| Bondtech Prusa Upgrade Extruder and Motor | 1 | |
| Dowel pin<br/>diameter: 3mm, length: 15mm to 15.8mm | 1 | Must fit the 2GT idler bearing.<br/>:pushpin: Cut a M3 screw if you can't find one |
| M3 Hex nylock nuts (DIN 985) | 2 | |
| M3 Hex nuts (DIN 934) | 3 | |

### Printed parts

Download the printed parts corresponding to your Bondtech extruder version (hotend and Prusa).

For **E3D v6** hotend:
  * MK2S : [bear_bondtech_e3d_mk2s_mk2.5.zip](printed_parts/bear_bondtech_e3d_mk2s_mk2.5.zip?raw=true)
  * MK2.5 : [bear_bondtech_e3d_mk2s_mk2.5.zip](printed_parts/bear_bondtech_e3d_mk2s_mk2.5.zip?raw=true)
  * MK2.5S : [bear_bondtech_e3d_mk2.5s.zip](printed_parts/bear_bondtech_e3d_mk2.5s.zip?raw=true)
  * MK3 : [bear_bondtech_e3d_mk3.zip](printed_parts/bear_bondtech_e3d_mk3.zip?raw=true)
  * MK3S : [bear_bondtech_e3d_mk3s.zip](printed_parts/bear_bondtech_e3d_mk3s.zip?raw=true)

For **Slice Engineering Mosquito** hotend:
  * MK2.5S : [bear_bondtech_mosquito_mk2.5s.zip](printed_parts/bear_bondtech_mosquito_mk2.5s.zip?raw=true)
  * MK3S : [bear_bondtech_mosquito_mk3s.zip](printed_parts/bear_bondtech_mosquito_mk3s.zip?raw=true)

### Print settings

:warning: Warning: The parts have been designed and tested with the parameters below and it is important to follow them to avoid issues like part cracking, bad bridging, not enough stiffness or wrong tolerances. Be sure to have a well calibrated machine and extruder. Check our guide here for [calibrating extrusion multiplier](https://guides.bear-lab.com/Guide/Extrusion+multiplier+and+filament+diameter/8?lang=en)

  * Slicer : PrusaSlicer recommended
  * Infill type : Gyroid recommended
  * Support : No
  * Brim : No
  * Detect thin walls : No
  * Perimeters width (internal and external) : 0.45mm

| Part | Quantity | Layer Height | Infill | Perimeters | Top/Bottom Layers | Filament Type |
|:-----|:---:|:---:|:---:|:---:|:---:|:---:|
| bondtech_x_carriage_mkX.stl | 1 | 0.20mm | 20% | 4 | 5 | PETG |
| x_end_idler | 1 | 0.20mm | 20% | 4 | 5 | PETG |
| x_end_idler_tensioner | 1 | 0.20mm | 20% | 4 | 5 | PETG |
| x_end_motor | 1 | 0.20mm | 20% | 4 | 5 | PETG |
| cable_guide_back_a | 1 | 0.20mm | 20% | 4 | 5 | PETG |
| cable_guide_back_b | 1 | 0.20mm | 20% | 4 | 5 | PETG |
| x_carriage_back | 1 | 0.20mm | 20% | 3 | 5 | PETG |

You can find more details about recommended filaments in on our [FAQ](https://guides.bear-lab.com/Wiki/Bear_FAQ).

### Assembly Guide

The assembly guide is available on [this page of guides.bear-lab.com](https://guides.bear-lab.com/Guide/Assembly+Guide/40).

### Source

All source files in Fusion 360 and STEP format can be [download here](source/bondtech_x_carriage_source.zip?raw=true).

### Thank you

Thank you to Bondtech for having listen several of my design propositions for this extruder. Thank you to the BPE2000 group for the chat and support.

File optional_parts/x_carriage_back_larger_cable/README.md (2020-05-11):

# Bear X Axis And Extruder (BearExxa)

## X carriage back for larger filament sensor cable

This is a remix of the original Bear extruder X carriage back to allow use of larger cables like the MK2.5/MK3 laser filament sensor cable (for [Bondtech X carriage](../bondtech_x_carriage) for example).

Left is standard X carriage back and right is the larger one proposed here.

Use the links below to download the STL:
  * For MK2.5(S): [x_carriage_back_mk2.5_larger_cable.stl](printed_parts/x_carriage_back_mk2.5_larger_cable.stl?raw=true)
  * For MK3(S): [x_carriage_back_mk3_larger_cable.stl](printed_parts/x_carriage_back_mk3_larger_cable.stl?raw=true)

  X carriage backs

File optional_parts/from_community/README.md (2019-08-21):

# Bear X Axis And Extruder

## Optional parts made by the community

Designed by the community. Huge thank you all, you are making this extruder even better!

| Description | Author | Link |
|:---:|:---:|:----:|
| E3D Volcano Extruder for MK3 Bear conversion | ufoDziner | https://www.thingiverse.com/thing:3166998 |
| Serious business Bear X-axis replacement | zbrozek | https://www.thingiverse.com/thing:3194456 |
| Big Bearing Bear X-Axis end | ufoDziner | https://www.thingiverse.com/thing:3243705 |
| Bear X end motor with bearing support | ilya_tsaryuk | https://www.thingiverse.com/thing:3249583 |
| Bear Extruder BLTouch Mount | vertigo235 | https://www.thingiverse.com/thing:3251530 |
| Y-Axis Bearing holders | MartinMajewski | https://www.thingiverse.com/thing:3342147 |
| Bear Extruder MK2S based on 0.6.0-alpha | Ringo1508 |https://www.thingiverse.com/thing:3252121 |
| Bear extruder with hobbed pulley from MK2S | toto99303 | https://www.thingiverse.com/thing:3661475 |
| MMU2S Door Sensor for Bear Extruder | vertigo235 | https://www.thingiverse.com/thing:3472911 |
| Nema 17 Gearbox "Pullybox" Mod for Extruder | vertigo235 | https://www.thingiverse.com/thing:3714978 |
| Bear extruder for Slice Mosquito Hotend | Ben's 3D | https://www.thingiverse.com/thing:3733768 |
| Filament cover for Palette 2 | CheshirePirat | https://www.thingiverse.com/thing:3803392 |

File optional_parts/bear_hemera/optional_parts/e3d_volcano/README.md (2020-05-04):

# Bear X axis and Extruder

## E3D Volcano adapter for BearMera

### Table of contents
  1. [Introduction](#introduction)
  1. [Compatibility](#compatibility)
  1. [Bill Of materials](#bill-of-materials)
  1. [Printed parts](#printed-parts)
  1. [Assembly guide](#assembly-guide)
  1. [Source](#source)
  1. [Credit](#credit)

### Introduction

This is a body_front printed part to use [E3D Volcano](https://e3d-online.com/volcano-block-for-sensor-cartridges) with BearMera.

Bear Hemera Volcano

### Compatibility

This body_front is only compatible with Bear Hemera mount.

### Bill Of materials

#### Extra hardware from stock BearMera

This is the list of extra material you will need from original Prusa extruder and X axis.

| Part | Quantity<br>(pce) | Detail | Example Link |
|---|:---:|---|---|
| M3x8mm socket head screw (ISO 4762) | 1 | For front left Hemera t-nut | |
| M3x20mm socket head screw (ISO 4762) | 1 | For top screw of nozzle fan | |
| M3 Hex nuts (DIN 934) | 1 | | |

### Printed parts

Download all parts for BearMera and replace body_front.stl by body_front_volcano.stl.

  * Part body_front_volcano for BearMera: [body_front_volcano.stl](printed_parts/stl/body_front_volcano.stl?raw=true)
  * BearMera and X axis for MK2(S) and MK2.5(S): [bearmera_mk2_mk2s_mk2.5_mk2.5s.zip](../../printed_parts/bearmera_mk2_mk2s_mk2.5_mk2.5s.zip?raw=true)
  * BearMera and X axis for MK3(S) and MK3(S): [bearmera_mk3_mk3s.zip](../../printed_parts/bearmera_mk3_mk3s.zip?raw=true)

### Print settings

Use same [print settings as BearMera](../../README.md#print-settings)

### Assembly guide

Follow the BearMera assembly guide but with the E3D Volcano heatblock and the body_front_volcano.stl. Here are where the extra hardware should go:

Bear Hemera Volcano Assembly

### Source

Source file can be Downloaded here: [Fusion 360 file](source/bear_hemera_volcano.f3z?raw=true) or [STEP file](source/bear_hemera_volcano.step?raw=true) (you need to right-click and save as).

### Credit

Thank you very much to Flobler for having designed and tested this body_front_voclano part.

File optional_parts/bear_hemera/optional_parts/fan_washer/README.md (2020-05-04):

# Bear X axis and Extruder

## Fan washer for BearMera

### Table of contents
  1. [Introduction](#introduction)
  1. [Compatibility](#compatibility)
  1. [Bill Of Materials](#bill-of-materials)
  1. [Printed Parts](#printed-parts)
  1. [Assembly Guide](#assembly-guide)
  1. [Source](#source)

### Introduction

The original Hemera hotend fan has a tendency to twist if you tighten it too strongly. Those printed washers are solving this issue and let you secure more strongly the Hemera fan.

Bear Hemera Fan Washer

Bear Hemera Fan Washers

### Compatibility

Only compatible with Hemera hotend fans that have a counterbore on the back (side of the sicker's fan).

### Bill Of Materials

No extra hardware needed, you can use the original self tapping screws coming with your Hemera.

### Printed Parts

Download the part here: [fan_washer.stl](printed_parts/stl/fan_washer.stl?raw=true)

### Print settings

| Part | Quantity | Layer Height | Infill | Perimeters | Top/Bottom Layers | Filament Type |
|:----|:----:|:----:|:----:|:----:|:----:|:----:|
| fan_washer | 2 | 0.20mm | not relevant | 2 | 5 | PETG |

### Assembly Guide

Place one washer on each fan mounting screws. The washers should be on the back side of the fan, where the sticker is.

### Source

Source file can be Downloaded here: [Fusion 360 file](source/fan_washer.f3d?raw=true) or [STEP file](source/fan_washer.step?raw=true) (you need to right-click and save as).

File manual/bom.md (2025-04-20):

# Bear X axis and Extruder (BearExxa)

## Bill of Materials

### Hardware BOM For Prusa Printers

There are 5 revisions of Original Prusa extruder for MK2.5(S)/MK3(S) and they come with different screws and nuts, as well as different spare bag. Make sure to double check you have all the hardware listed in this table before starting.

| Parts | Quantity | Details | Example Links |
|---|:---:|---|---|
| Original Prusa i3 MK2.5S or MK3s printer | 1 | | [Prusa](https://www.prusa3d.com) |
| Dowel pin<br/>diameter: 2.90-2.95mm<br/>length: 15mm to 15.8mm | 1 | :pushpin: Cut a M3 screw if you can't find one | |
| M3x10mm socket head screw (ISO 4762) | 14 | | [McMaster-Carr](https://www.mcmaster.com/#91292a113/=1coixe5) |
| M3x14mm socket head screw (ISO 4762) | 4  | :warning: Use M3x16 button head (ISO 7380)<br/>for Sunon or Delta hotend fan | [McMaster-Carr](https://www.mcmaster.com/#91292a027/=1coixl3) |
| M3x18mm socket head screw (ISO 4762) | 14 | | [McMaster-Carr](https://www.mcmaster.com/#91292a029/=1coixwt) |
| M3x25mm socket head screw (ISO 4762) | 2  | | [McMaster-Carr](https://www.mcmaster.com/#91292a020/=1cok8ux) |
| M3x40mm socket head screw (ISO 4762) | 6  | | [McMaster-Carr](https://www.mcmaster.com/#91292a024/=1coj8pe) |
| M2x12mm socket head screw (ISO 4762) | 2  | :warning: MK2.5 only | [McMaster-Carr](https://www.mcmaster.com/#91292a834/=1cok8m8) |
| M3 Hex nuts (DIN 934) | 14 | | [McMaster-Carr](https://www.mcmaster.com/#91828a211/=1cojadu) |
| M3 Hex nylock nuts (DIN 985) | 4 | | [McMaster-Carr](https://www.mcmaster.com/#93625a100/=1d2yh4u) |
| M3 Square nuts (DIN 562) | 7 | 1.8mm thick and 5.5mm wide | |
| M3 Steel washer (DIN 125), 0.5mm thick | 5 | | |
| 50mm PTFE Tube<sup>1</sup> | 1 | Same PTFE tube than in MK2S,<br/>MK2.5 (non-S) and MK3 (non-S).<br/><br/>:pushpin: Check our guide: [Trim PTFE Tube] | |
| Zip ties 2.5x100mm | 6 | | |

> Note<sup>1</sup> : The printed parts include a PTFE cutter and the assembly will guide you on how to properly trim the PTFE tube. You can check our [Trim PTFE Tube] guide to ensure you have all the hardware to do it.

[Trim PTFE Tube]: https://guides.bear-lab.com/Guide/Trim+PTFE+Tube/21?lang=en

### Additional BOM for scratch build

| Parts | Quantity | Specifications | Example Links |
|---|:---:|---|---|
| Nema 17 stepper for X axis<br/>LDO 42STH38-1004A100CM | 1 | [Datasheet](https://github.com/gregsaun/bear_extruder_and_x_axis/tree/master/doc/datasheets/LDO-42STH38-1004A100CM-RevA-for-3D.pdf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) | [Prusa](https://shop.prusa3d.com/en/mk3mk3s/388-x-axis-stepper-motor.html) |
| Nema 17 stepper for Z axis<br/>integrated Lead screw Tr8x8 (P2x4) and nut<br/>LDO-42STH34-1004L321E100CM | 2 | [Datasheet](https://github.com/gregsaun/bear_extruder_and_x_axis/tree/master/doc/datasheets/LDO-42STH34-1004L321E100CM-RevA-for-3D.pdf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) | [Prusa](https://shop.prusa3d.com/en/spare-parts/386-stepper-motor-z-axis-right.html) |
| Nema 17 stepper for extruder extruder<br/>LDO Cool Power 42STH40-1004ASR | 1 | [Datasheet](https://github.com/gregsaun/bear_extruder_and_x_axis/tree/master/doc/datasheets/LDO-42STH40-1004ASR_cool_power.pdf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) | |
| Bondtech gears | 1 | 1.75mm/5.0mm<br/>with its 20mm shaft | [Bondtech](https://www.bondtech.se/en/product/drivegear-kits/) |
| Hotend E3D v6<br/>40W heater<br/>0.45mm nozzle | 1 | [E3D-Online](https://e3d-online.com/v6-all-metal-hotend)
| Hotend Fan | 1 | Check [our recommended fans](https://github.com/gregsaun/bear_extruder_and_x_axis/tree/master/optional_parts/hotend_fan) | |
| Nozzle Fan | 1 | Minimal specifications:<br/>- CFM: 3.8<br/>- Static Pressure: 11.3 mmH2O<br/>- Bearing type: ball bearing | [Prusa](https://shop.prusa3d.com/en/spare-parts/201-print-fan.html) |
| Inductive Sensor | 1 | Diameter of 8mm, length around 35mm | | [Prusa](https://shop.prusa3d.com/en/spare-parts/200-pinda-probe-v2.html) |
| Filament sensor<br/>with magnets, steel ball and cables | 1 | 1x IR Sensor: [GitHub Prusa](https://github.com/prusa3d/MKxS-IR-sensor)<br/>1x Steel ball 7mm diameter<br/>1x Magnet 20x6x2<br/>1x Magnet 10x6x2<br/> | [Prusa](https://shop.prusa3d.com/en/upgrades/898-original-prusa-i3-mk3-to-mk3s-upgrade-kit.html#) |
| 2GT 16T pulley | 1 | 5mm bore<br/> | [E3D-Online store](https://e3d-online.com/gates-powergrip-pulley-16-tooth-6mm) |
| 2GT 20T idler | 1 | 3mm bore<br/>smooth or toothed<br/>Check this [optional part for E3D idler](https://github.com/gregsaun/bear_extruder_and_x_axis/tree/master/optional_parts/x_end_idler_tensioner_e3d) | |
| Extruder spring | 1 | Wire Diameter: 0.8mm<br/>Centre Diameter: 4.9mm<br/>Free length: 15mm<br/>Compressed length: 10mm<br/>Material: DIN 2076-B | [Prusa](https://shop.prusa3d.com/en/mk3mk3s/599-tension-spring-1x.html) |
| Smooth rods | 2 | 8mm diameter H6<br/>370mm long | [Prusa](https://shop.prusa3d.com/en/mk3mk3s/589-smooth-rod-8x370-x-axis-1-piece.html) |
| LM8UU bearings | 3 | [Prusa](https://shop.prusa3d.com/en/mk3mk3s/140-linear-bearing-lm8uu.html) |
| Gates LL-2GT RF belt | 1 | 6mm width<br/>880mm long | [E3D-Online](https://e3d-online.com/gates-powergripr-gt2-belt-6mm-x-100mm) |
| Nylon cable<br/>2.85-3.00mm diameter<br/>500mm long | 1 | Check 2.85mm filament samples or 2.85mm cleaning filaments | |

:pushpin: : You need to have ordered a Prusa printer and need to login on Prusa store to see the articles. You can probably find this hardware from our [official distributors](https://github.com/gregsaun/prusa_i3_bear_upgrade/blob/master/README.md#where-can-i-get-an-official-kit)

### Printed Parts BOM

| Parts | Quantity |
|---|:---:|
| cable_guide_back_a | 1 |
| cable_guide_back_b | 1 |
| extruder_body | 1 |
| extruder_cover | 1 |
| extruder_idler_bondtech | 1 |
| filament_sensor_cover | 1 |
| hotend_collet_clip | 1 |
| x_carriage | 1 |
| x_carriage_back | 1 |
| x_end_idler | 1 |
| x_end_idler_idler_mount | 1 |
| x_end_motor | 1 |

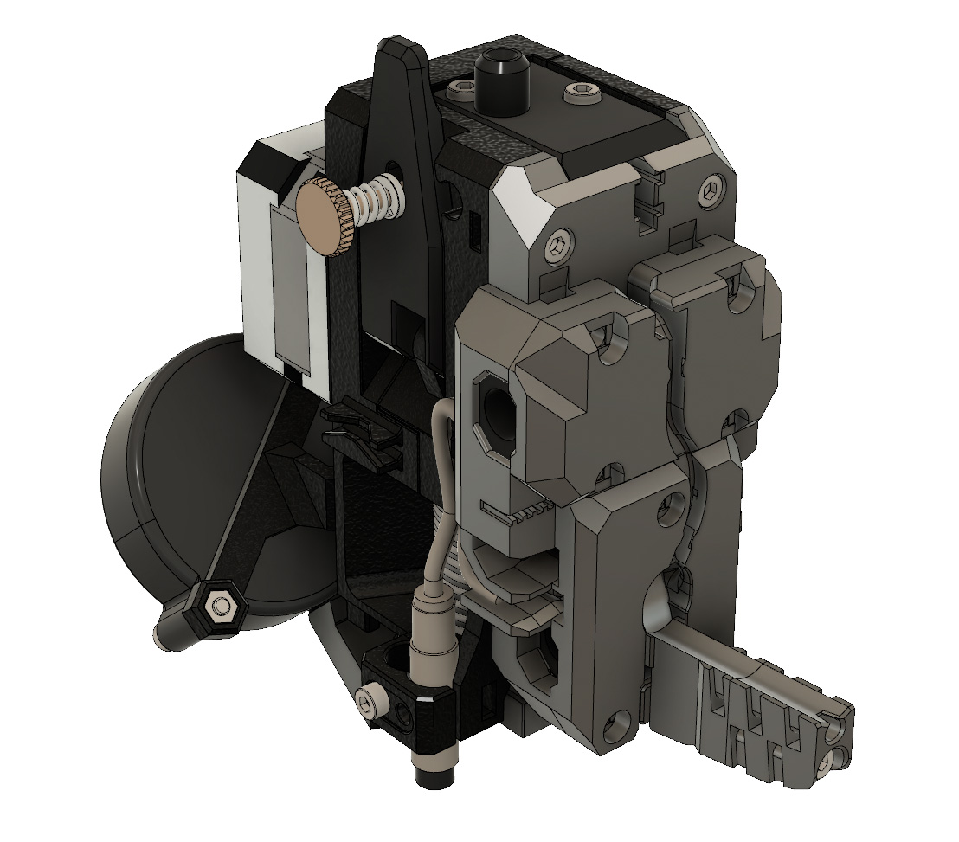
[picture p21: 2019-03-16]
optional_parts/bondtech_x_carriage/images/bondtech_bear-X-axis_01.jpg

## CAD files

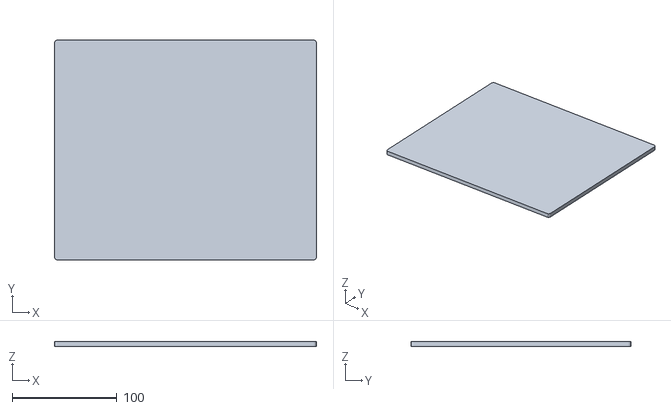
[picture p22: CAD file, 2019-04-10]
test/full_surface_bed/bear_full_surface_bed.stl
250.0 x 210.0 x 5.00

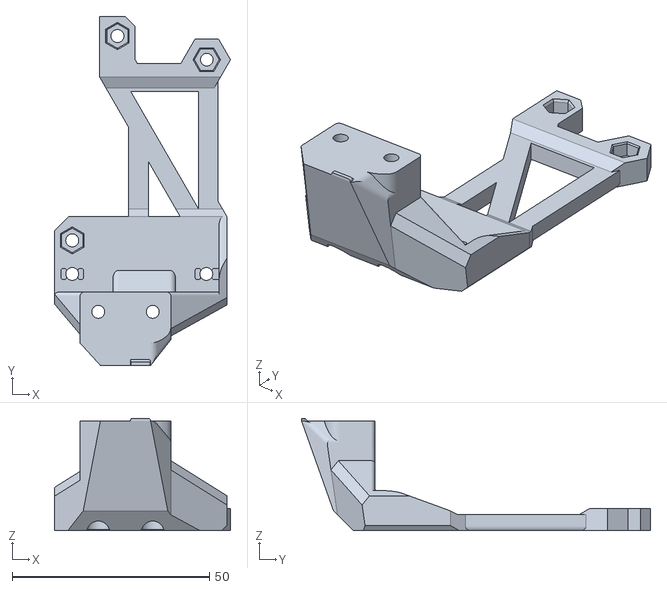
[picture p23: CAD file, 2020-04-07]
optional_parts/bear_hemera/optional_parts/e3d_volcano/printed_parts/stl/body_front_volcano.stl
44.6 x 88.4 x 28.4

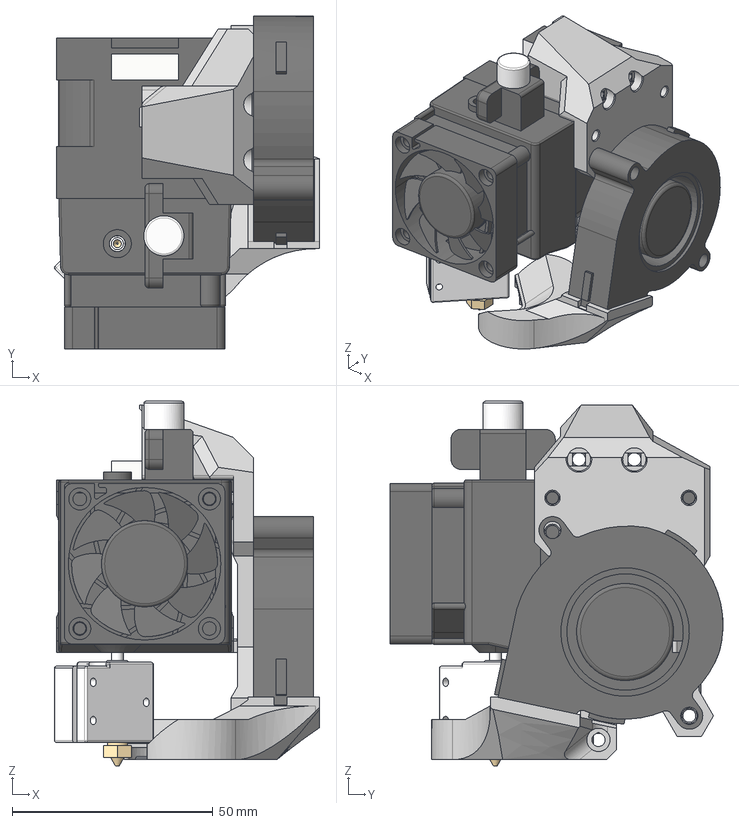
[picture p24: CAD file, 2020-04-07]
optional_parts/bear_hemera/optional_parts/e3d_volcano/source/bear_hemera_volcano.step
66.1 x 83.0 x 90.8 mm
stepper
heatsink
hemera_heatbreak
e3d_hemera_fan
volcano_heaterblock
volcano_nozzle
body_front_volcano
nozzle_fan_1
duct
support

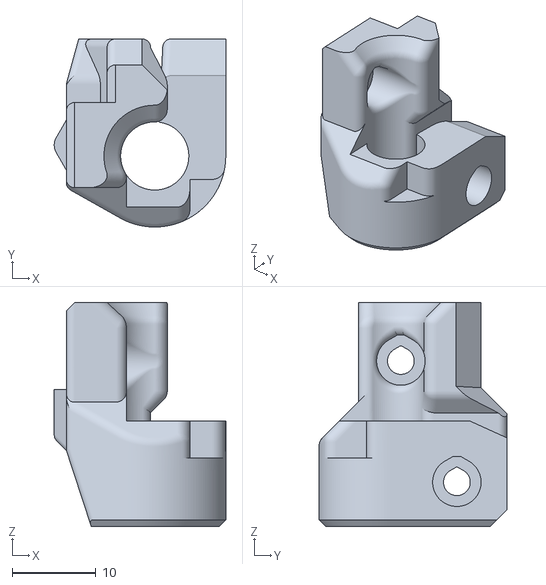
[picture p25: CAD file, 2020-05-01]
optional_parts/bear_hemera/printed_parts/stl/common_to_all_versions/pinda_mount.stl
20.5 x 22.5 x 26.8

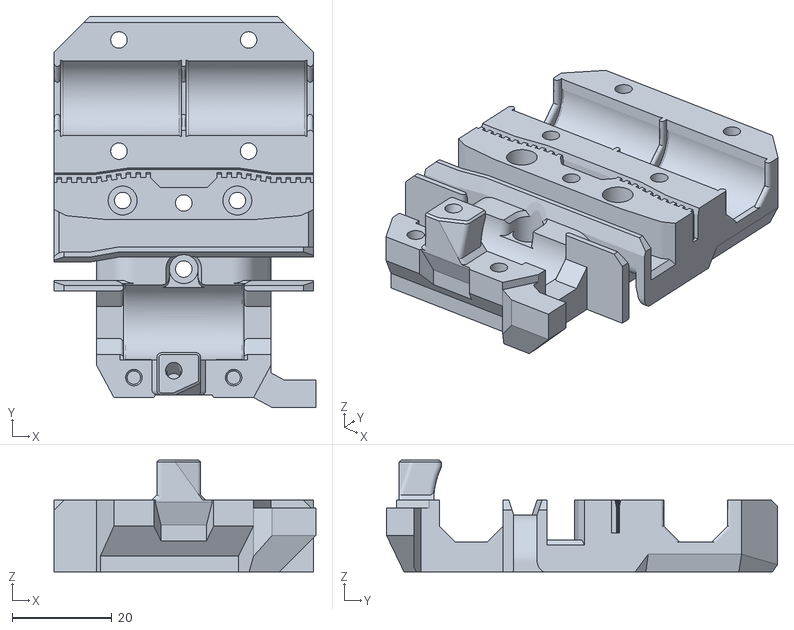
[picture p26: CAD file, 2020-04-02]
optional_parts/bear_hemera/printed_parts/stl/mk2_mk2s_mk2.5_mk2.5s/x_carriage.stl
52.5 x 78.4 x 22.4

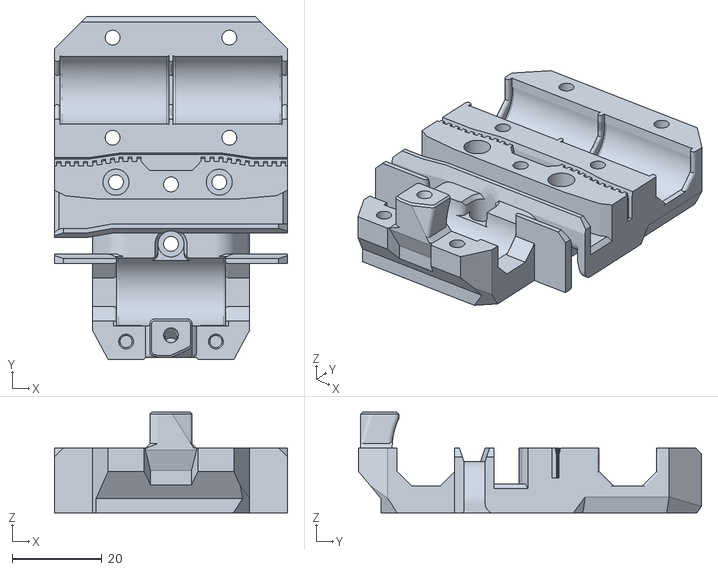
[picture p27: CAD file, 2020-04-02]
optional_parts/bear_hemera/printed_parts/stl/mk3_mk3s/x_carriage.stl
52.0 x 76.4 x 22.4

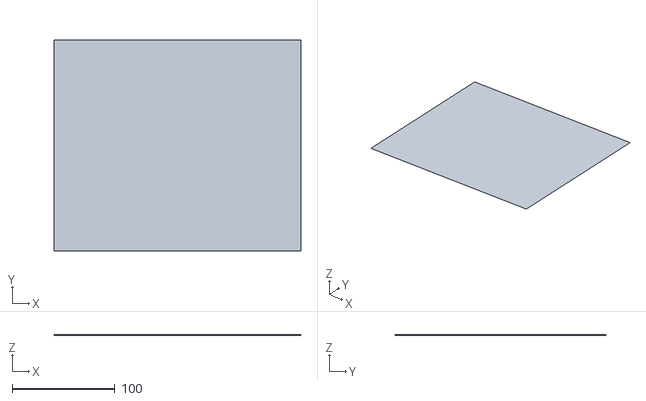
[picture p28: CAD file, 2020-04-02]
optional_parts/bear_hemera/test/print_surface/print_surface_240x205_mk2.5-2.5s-3-3s.stl
240.0 x 205.0 x 0.2

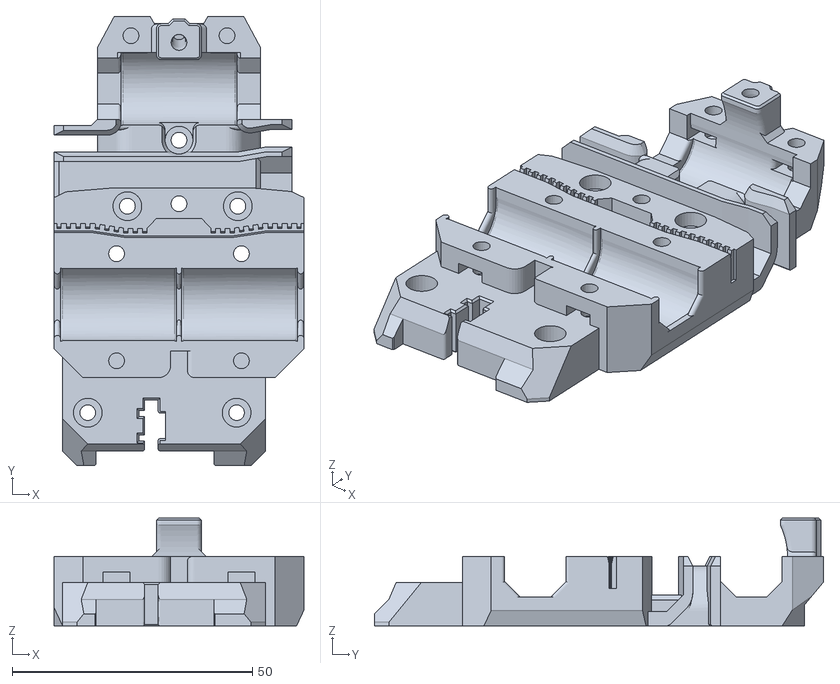
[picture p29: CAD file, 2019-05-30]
optional_parts/bondtech_x_carriage/printed_parts/bondtech_x_carriage_mk3_mk3s.stl
52.0 x 93.5 x 22.4

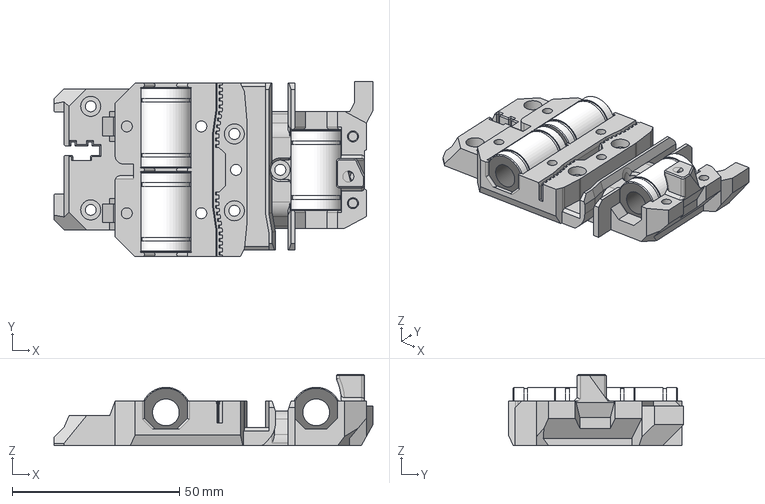
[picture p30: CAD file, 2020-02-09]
optional_parts/bondtech_x_carriage/source/bondtech_e3d_x_carriage_mk2s_mk2.5.step
95.5 x 52.5 x 21.4 mm
lm8uu x 3
x_carriage

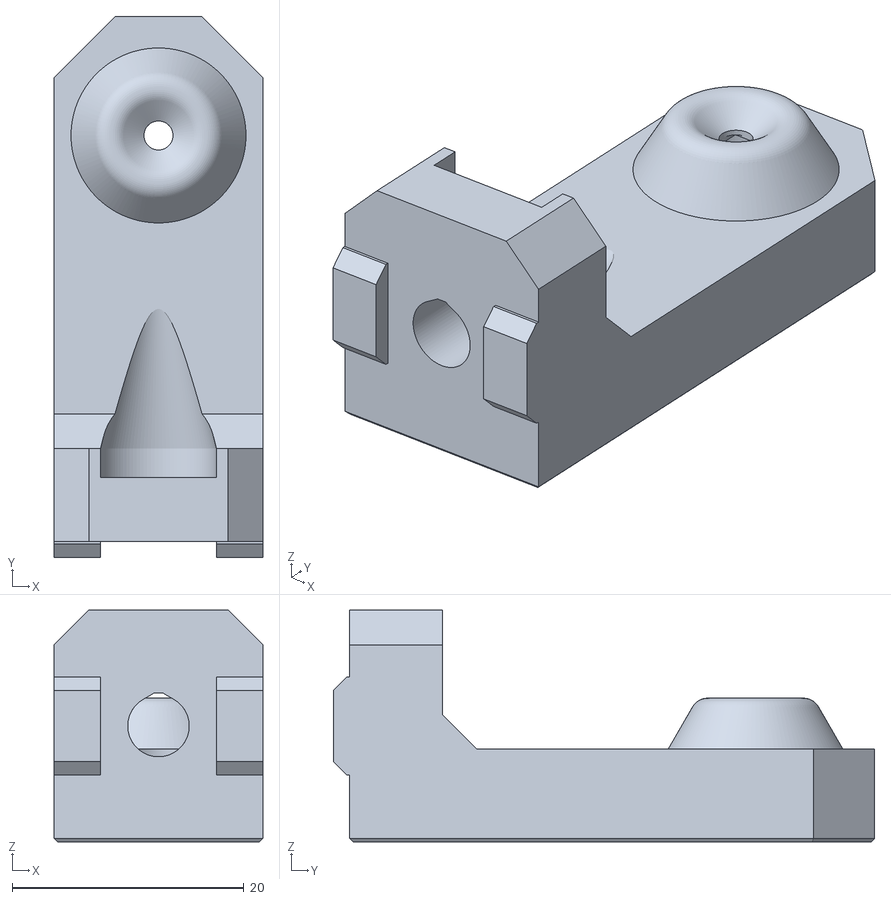
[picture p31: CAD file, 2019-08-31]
optional_parts/reverse_bowden/printed_parts/vslot_mount_pc4-m10_angled.stl
18.0 x 46.7 x 20.0

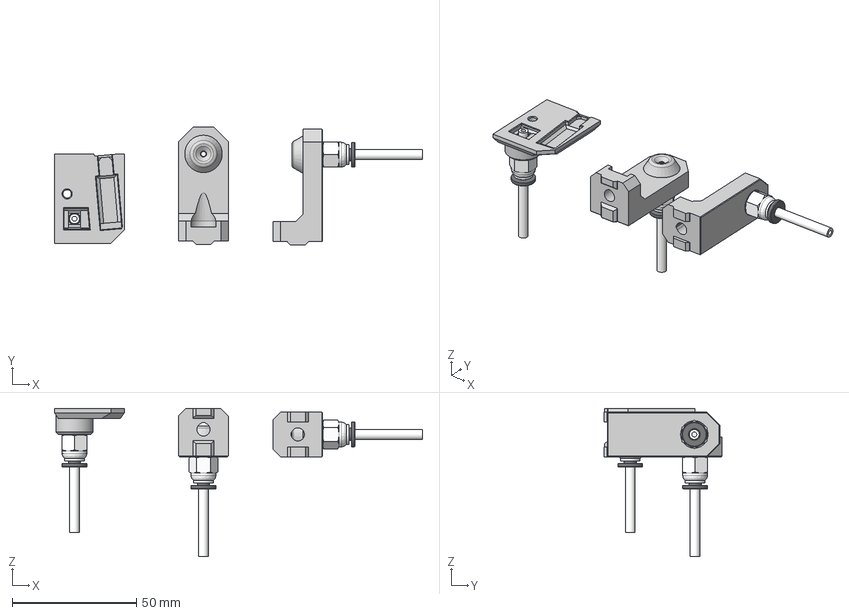
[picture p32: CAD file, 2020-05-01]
optional_parts/reverse_bowden/source/reverse_bowden.step
148.2 x 47.6 x 59.7 mm
vslot_mount_pc4-m10
vslot_mount_pc4-m10_angled
fs_cover_pc4-m10_mk25s_mk3s
pc4-m10 x 3
ptfe x 3

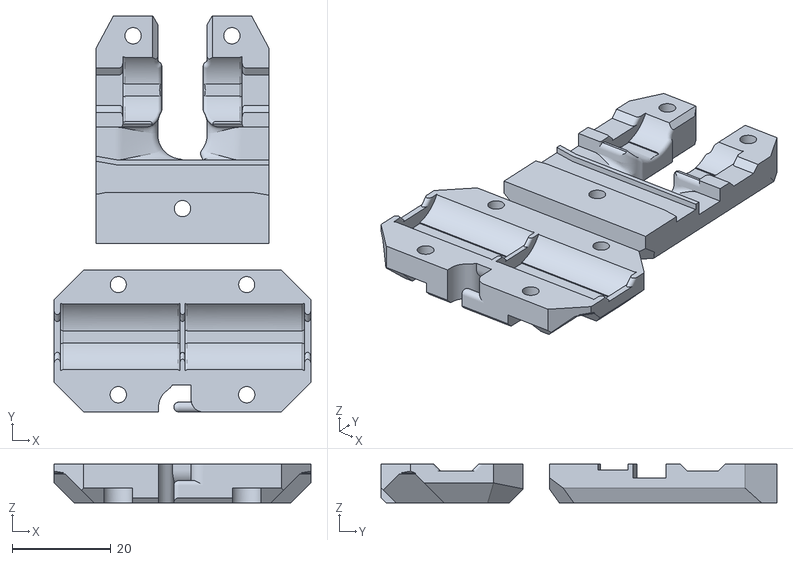
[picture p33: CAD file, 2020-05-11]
optional_parts/x_carriage_back_larger_cable/printed_parts/x_carriage_back_mk3_larger_cable.stl
52.0 x 80.2 x 7.80

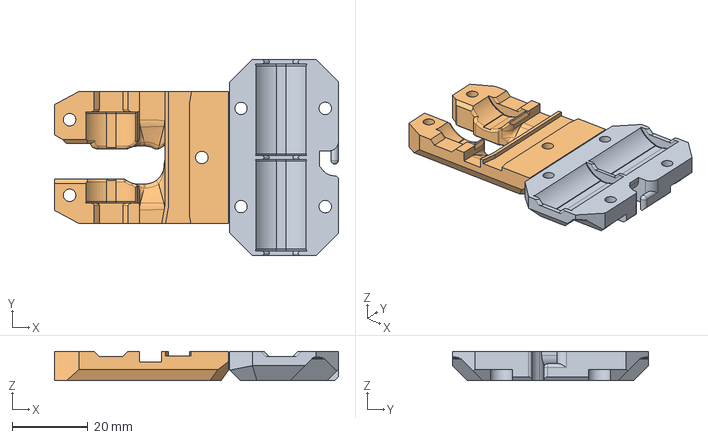
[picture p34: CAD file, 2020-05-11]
optional_parts/x_carriage_back_larger_cable/source/x_carriage_back_mk2.5_larger_cable.step
75.2 x 52.0 x 7.80 mm

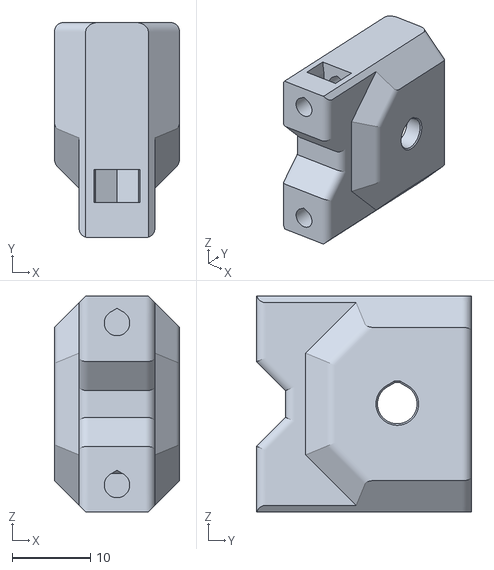
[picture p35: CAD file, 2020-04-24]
optional_parts/x_end_idler_tensioner_e3d/printed_parts/x_end_idler_tensioner_e3d.stl
16.0 x 27.5 x 27.6

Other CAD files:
optional_parts/bondtech_x_carriage/printed_parts/stl/bondtech_e3d_x_carriage_mk3.stl
optional_parts/x_end_idler_tensioner_e3d/source/e3d_idler_mount.step
printed_parts/stl/common/extruder_cover.stl
printed_parts/stl/common_to_all_versions/cable_guide_back_b.stl
optional_parts/bear_hemera/optional_parts/fan_washer/printed_parts/stl/fan_washer.stl
optional_parts/bear_hemera/optional_parts/fan_washer/source/fan_washer.f3d
optional_parts/bear_hemera/optional_parts/fan_washer/source/fan_washer.step
optional_parts/bear_hemera/printed_parts/stl/common_to_all_versions/body_back.stl
optional_parts/bear_hemera/printed_parts/stl/common_to_all_versions/body_front.stl
optional_parts/bear_hemera/printed_parts/stl/common_to_all_versions/cable_cover.stl
optional_parts/bear_hemera/printed_parts/stl/common_to_all_versions/nozzle_fan_duct.stl
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

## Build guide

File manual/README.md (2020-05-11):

# Bear X axis and Extruder Manual (BearExxa)

## Table of Content

1. [Bill Of Material](bom.md)
1. [Print Settings](print_settings.md)
1. [Printed Parts STL](../printed_parts)
1. [Assembly Guide](https://guides.bear-lab.com/c/Extruder_X_Axis)
1. [Optional Parts](../optional_parts)
1. [Sources](../src)

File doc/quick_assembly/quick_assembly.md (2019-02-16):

# Bear X axis and Extruder

## Quick assembly

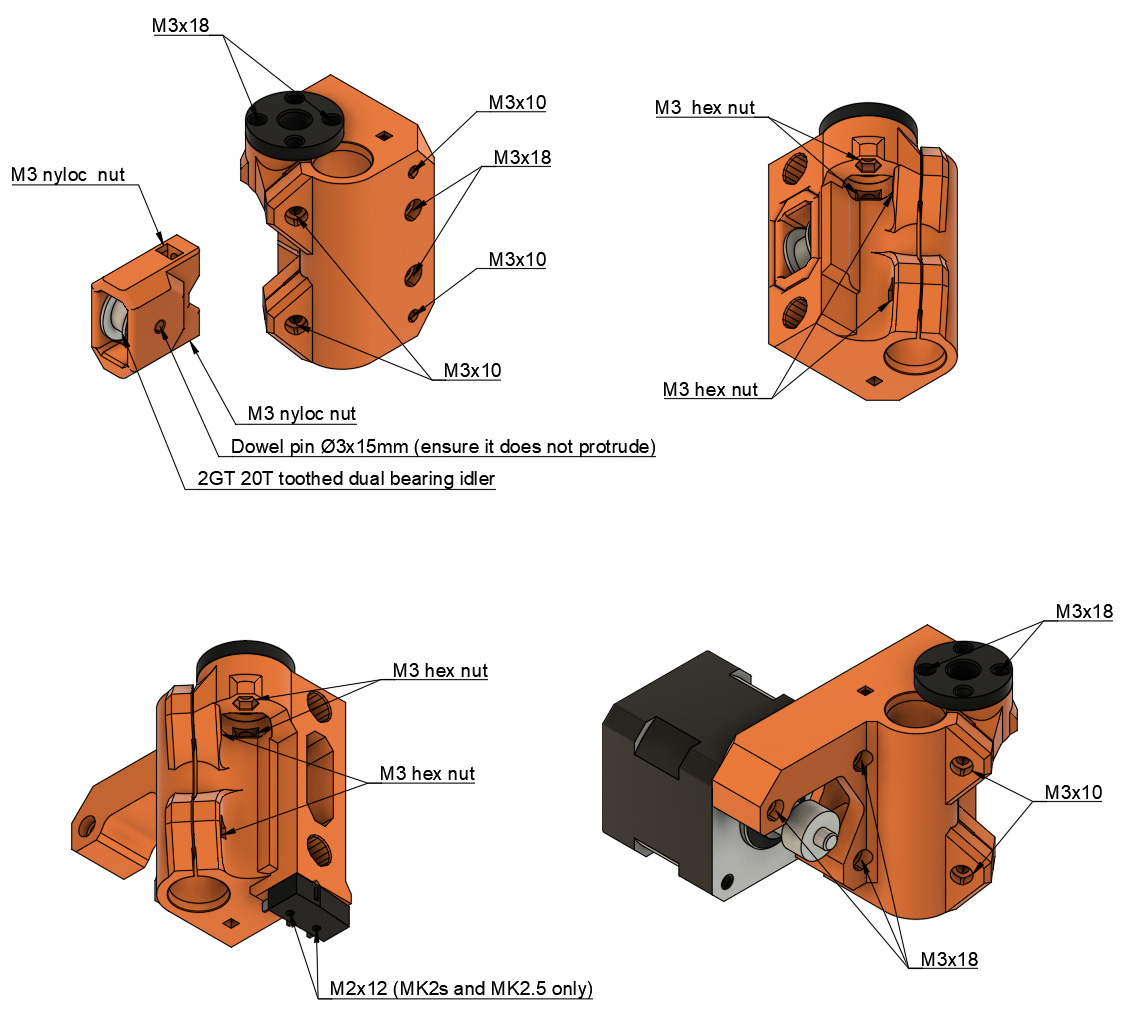
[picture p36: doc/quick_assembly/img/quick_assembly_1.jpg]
Quick assembly 1


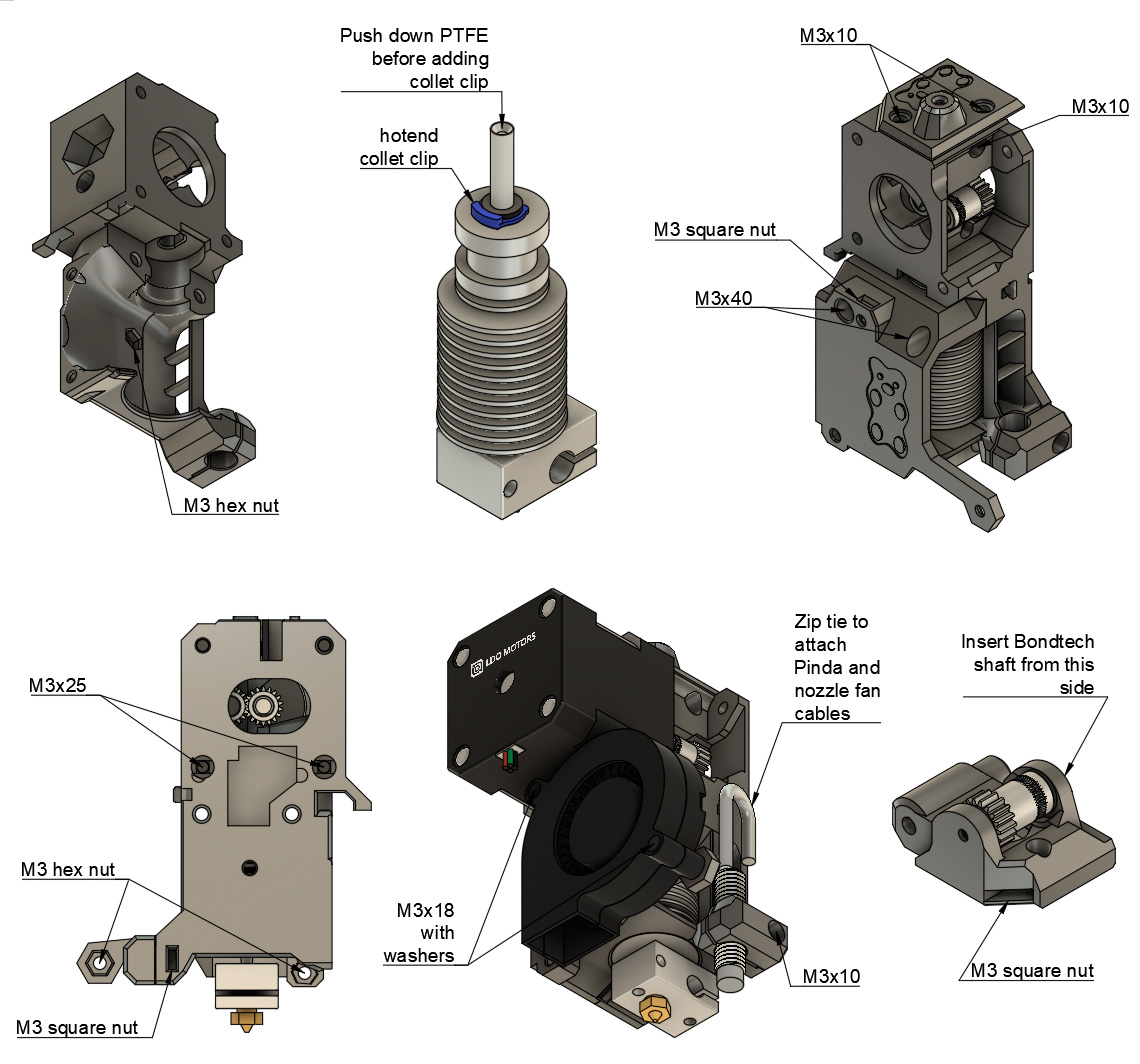
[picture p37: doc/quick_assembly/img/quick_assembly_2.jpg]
Quick assembly 2


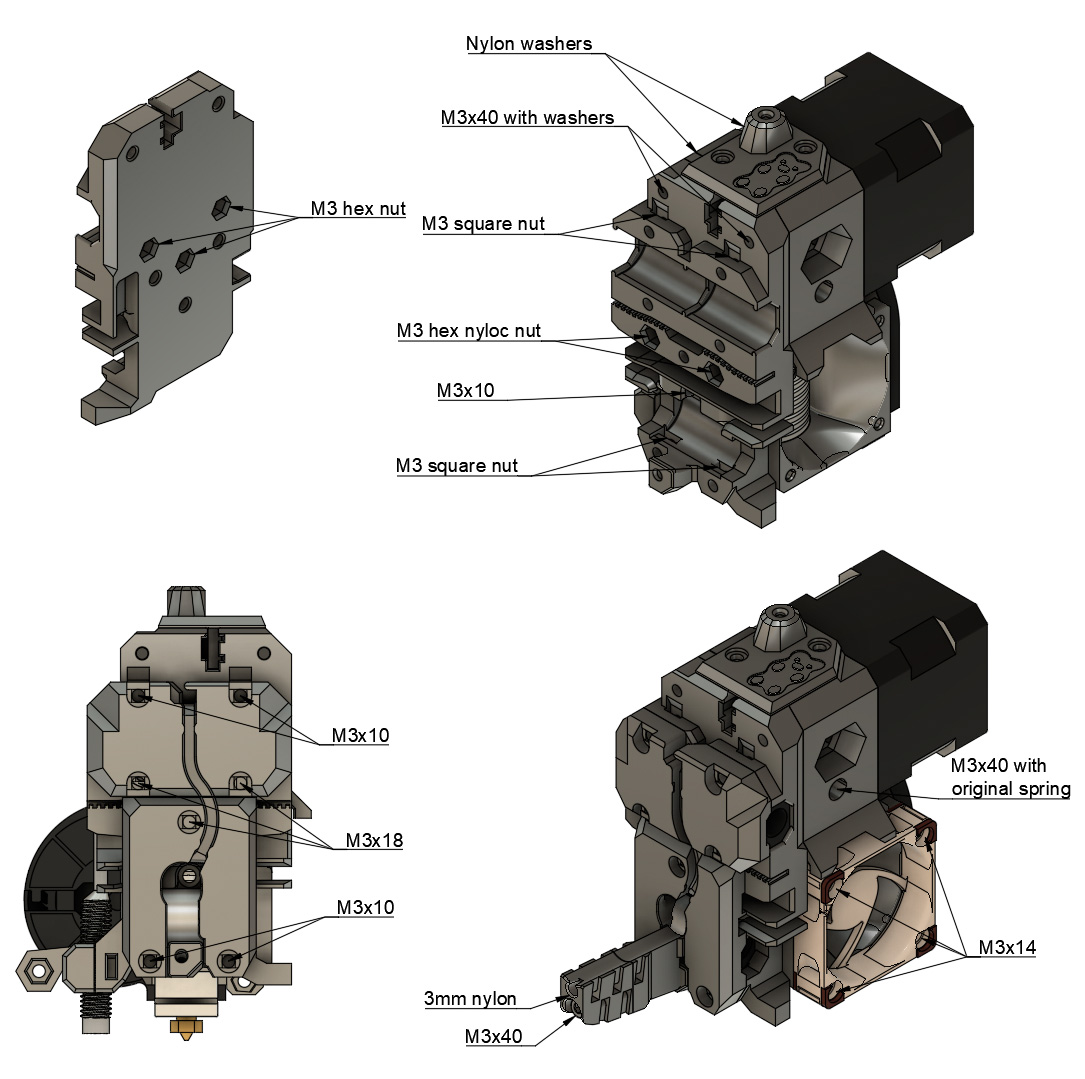
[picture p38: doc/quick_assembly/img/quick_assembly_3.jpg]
Quick assembly 2


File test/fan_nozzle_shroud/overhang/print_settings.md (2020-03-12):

# Hardware

  * Heatblock sock : no
  * Part position : center of bed
  * Nozzle : E3D 0.4mm

# Slicer

  * Slicer: PrusaSlicer
  * Layer height : 0.2mm
  * Perimeters : 2
  * Infill : 15%
  * Solid layers : 3 tops, 4 bottoms
  * Infill type : Rectilinear
  * Support : No
  * Brim : No
  * Detect thin walls : No
  * Ensure vertical shell thickness : Yes
  * Perimeters width (internal and external) : 0.45mm

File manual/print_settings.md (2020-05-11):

# Bear X axis and Extruder (BearExxa)

## Print Settings

:warning: Warning: The parts have been designed and tested with the parameters below and it is important to follow them to avoid issues like part cracking, bad bridging, not enough stiffness or wrong tolerances. Be sure to have a well calibrated machine and extruder. Check our guide here for [calibrating extrusion multiplier](https://guides.bear-lab.com/Guide/Extrusion+multiplier+and+filament+diameter/8?lang=en)

  * Slicer : PrusaSlicer recommended
  * Infill type : Gyroid recommended
  * Support : No
  * Brim : No
  * Detect thin walls : No
  * Perimeters width (internal and external) : 0.45mm

| Part | Quantity | Layer Height | Infill | Perimeters | Top/Bottom Layers | Filament type | Color |
|:----|:----:|:----:|:----:|:----:|:----:|:----:|:----:|
| cable_guide_back_a | 1 | 0.20mm | 20% | 4 | 5 | PETG | |
| cable_guide_back_b | 1 | 0.20mm | 20% | 4 | 5 | PETG | |
| extruder_body | 1 | 0.20mm | 20% | 4 | 5 | PETG | Black |
| extruder_cover | 1 | 0.20mm | 20% | 4 | 5 | PETG | |
| extruder_idler | 1 | 0.20mm | 20% | 4 | 5 | PETG | |
| filament_sensor_cover  | 1 | 0.20mm | 20% | 4 | 5 | PETG | Black |
| filament_sensor_lever  | 1 | 0.20mm | 20% | 4 | 5 | PETG<sup>1</sup> | Black |
| hotend_collet_clip | 1 | 0.20mm | 20% | 3 | 5 | PETG | |
| nozzle_fan_duct | 1 | 0.20mm | 20% | 3 | 5 | Read note<sup>2</sup> below | |
| ptfe_cutter_50mm_60deg | 1 | 0.20mm | 20% | 3-4 | 5 | PETG | |
| x_carriage | 1 | 0.20mm | 20% | 4 | 5 | PETG | |
| x_carriage_back | 1 | 0.20mm | 20% | 3 | 5 | PETG | |
| x_end_idler | 1 | 0.20mm | 20% | 4 | 5 | PETG | |
| x_end_idler_tensioner  | 1 | 0.20mm | 20% | 4 | 5 | PETG | |
| x_end_motor | 1 | 0.20mm | 20% | 4 | 5 | PETG | |

> Note<sup>1</sup>: Avoid eSUN PETG as some user reported that it might not block IR signal correctly. No other PETG have been reported to have this issue yet.

> Note<sup>2</sup>: The nozzle_fan_duct needs to be printed with a heat resistant filament like ABS, Extrudr GreenTec Pro, annealed HTPLA, PC and probably much more. Don't forget to compensate for shrinkage accordingly to the filament type you are using.

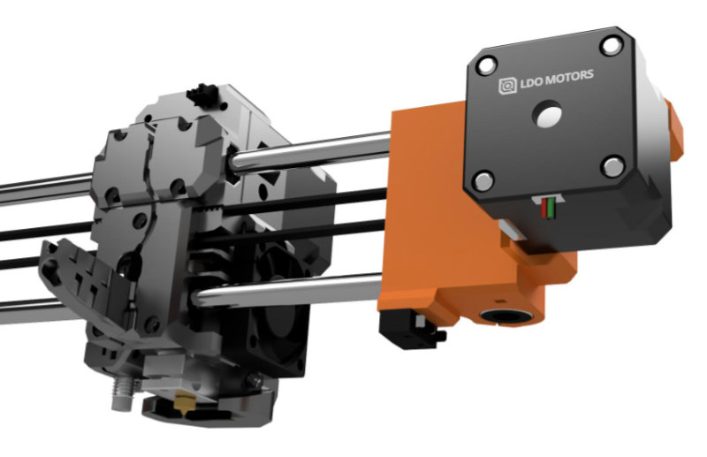
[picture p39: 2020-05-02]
doc/rendering/full_assembly_02_800px.jpg

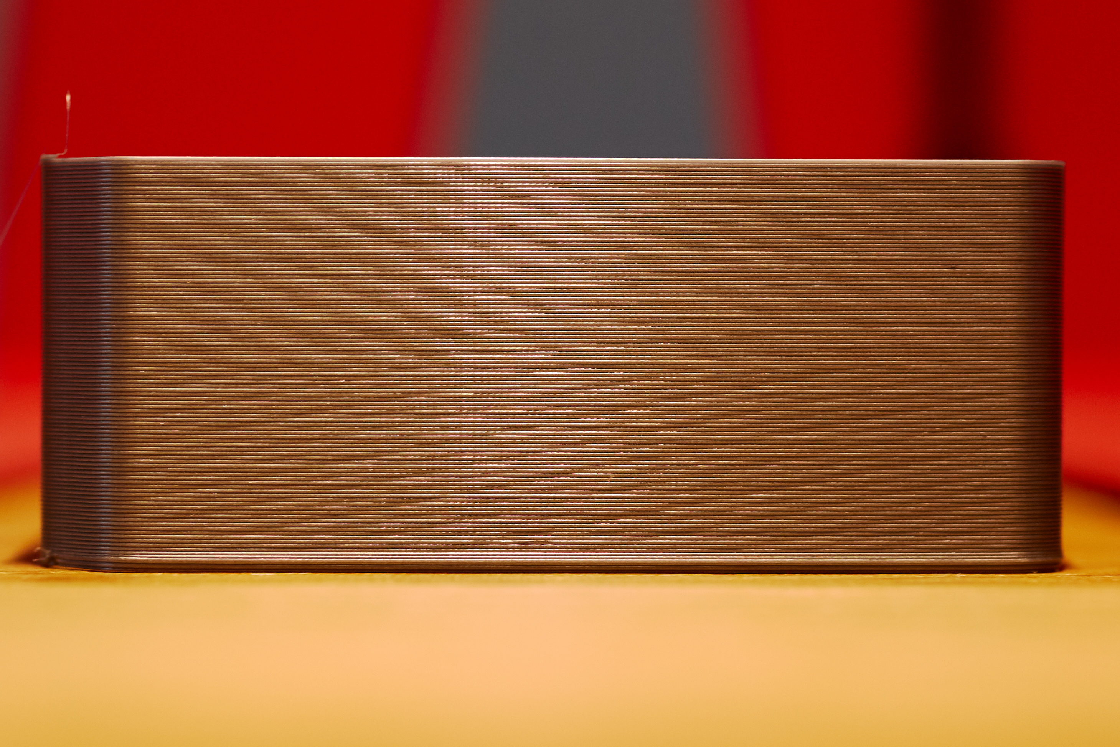
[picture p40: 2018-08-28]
test/inconsistent_extrusion/50x50x30mm_single_perimeter/photos/extruder_multiplier_change_mid_print.gcode.jpg

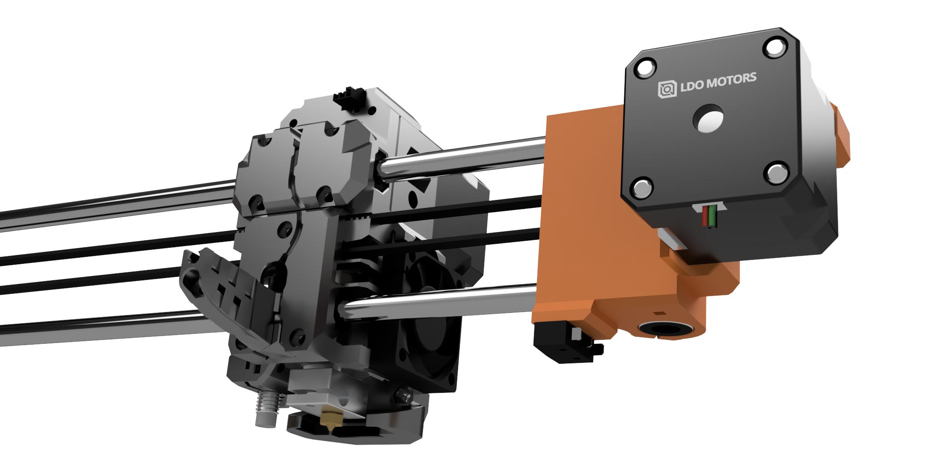
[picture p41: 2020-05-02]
doc/rendering/full_assembly_02.jpg

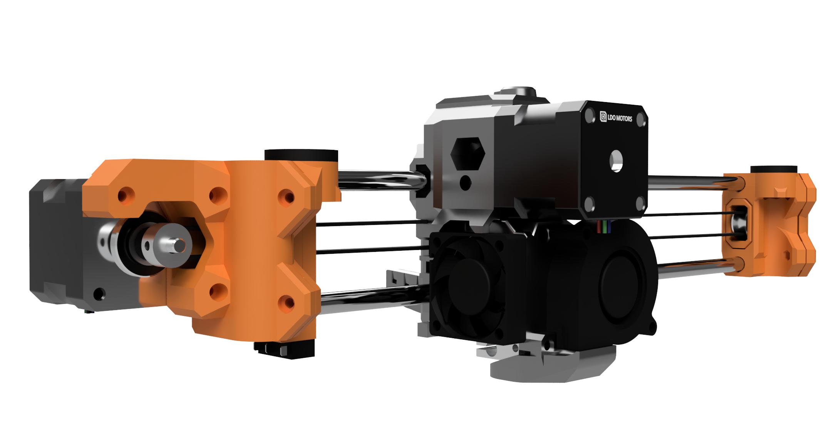
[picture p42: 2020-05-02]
doc/rendering/full_assembly_01.jpg

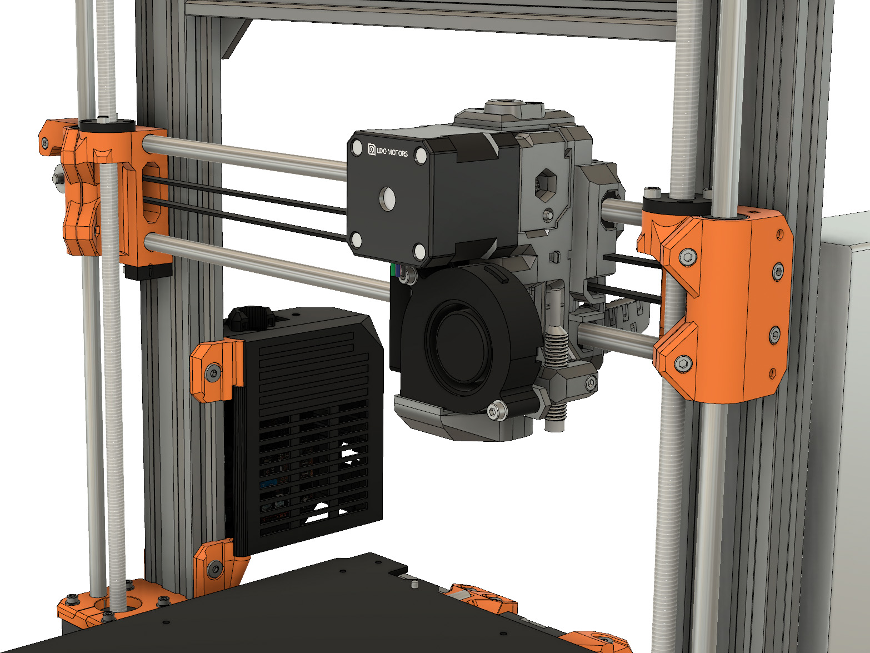
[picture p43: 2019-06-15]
doc/rendering/full_printer_mk3s_02.jpg

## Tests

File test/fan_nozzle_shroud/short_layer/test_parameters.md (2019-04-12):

# Environment
  * room temp stable, recommended between 23-25
  * semi enclosure

# Test method
  * insert the spike in the tool with the seam facing up
  * don't push the spike in, just lay it in
  * using a caliper, measure the distance between the lower face of the top rectangle hole and the bottom of spike

If the effect is not enough pronounced increase print temp or print faster.

# Print settings for the tool

## Layers and shells
  * Layer height 0.15mm
  * 3 perimeters
  * 5 tops/bottoms    

# Print settings for the spike

## Material
  * PLA, HTPLA or HTPLA+
  * semi enclosure
  * room temp around 23-25°C

## Layers and shells
  * Layer height 0.2mm
  * 2 perimeters
  * 3 tops/bottoms
  * 10% grid infill
  * Seam positions: rear

## Print speed
  * 50 mm/s perimeters
  * 25 mm/s small perimeters
  * 35 mm/s external perimeters
  * 60 mm/s infill

## Cooling
    * Fan at 100%
    * Enable fan if layer print time is below 100s
    * Slow down if layer print time is below 20s
    * Min print speed 15 mm/s

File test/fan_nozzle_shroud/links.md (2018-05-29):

Interesting reading:
http://www.desiquintans.com/coolingtests
http://www.desiquintans.com/coolingtests2
from same guy : https://www.thingiverse.com/thing:2770372

Dual blower:
http://scheuten.me/?p=1493

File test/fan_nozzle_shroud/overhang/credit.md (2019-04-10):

Inspired by the test tool from robrps
https://www.thingiverse.com/robrps/about

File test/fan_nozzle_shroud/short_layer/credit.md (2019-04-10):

Inspired by the work of Desi Quintans
http://www.desiquintans.com/coolingtests2

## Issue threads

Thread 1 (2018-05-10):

Installation of extruder onto x-carriage is difficult due to missing zip ties

gregsaun, 2018-05-10:
This is something I am working on it, I would like to try to split the x-carriage-back into to two pieces. Not sure it will be possible.

albegouws, 2018-05-20:
What about a temporary install helper just using the top two screws that hold the top bearings together?

gregsaun, 2018-05-22:
yes this is another possibility in case I cannot make the back in two parts

gregsaun, 2018-08-06:
Solved with release 0.40-alpha

Closed 2018-08-06.

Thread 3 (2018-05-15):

Suggestion - RJ4JP

albegouws, 2018-05-15:
Where you use Igus bearings would it be beneficial to have fine extrusions in the bearing spaces to ensure a better fit?  In the gaps where the bearing would have a clip fitting?

gregsaun, 2018-05-15:
I can make it a bit more tight but the way the part is printed (and the fact that customer's printer will have different calibration) will make impossible to have the perfect fit for Igus bearing. Igus needs an aluminum case with tight tolerance to be properly mounted.

albegouws, 2018-05-15:
Good point.  I’ll give a shot anyway and see how it turns out.  Are you planning any major commits soon?  I’ll try and print the parts this weekend for my Mk2.5 Bear 😉

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

gregsaun, 2018-05-15:
I will push new commits in few minutes ;-)

Closed 2018-06-07.

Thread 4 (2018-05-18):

Cable guide back a - difficult print

albegouws, 2018-05-18:
Printing the parts right now, the a part of the cable guide in the default orientation is a very difficult print to do successfully, the initial two or so layers are only time little marks on the bed, after a few layers it comes loose - depending on speed obviously. You can rotate and print at an angle but I think the one side could be flattened to print easier?

Will let you know how the rest goes, MK3 and Mk2.5 running at full speed.

gregsaun, 2018-05-20:
Cable guide back a and b need to be printed with other parts because they are very small. However I think I can use another orientation, I'll give a try ;-)

albegouws, 2018-05-20:
I flipped it on the flat side and adjusted angle to 5 degrees.

________________________________
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

gregsaun, 2018-05-26:
Hello, I did see that my parts was really not correctly aligned and I was thinking that you were asking another orientation. Sorry for the inconveniences!

I am going to fix it now and make it just a bit wider too

gregsaun, 2018-05-26:
Done! Thanks for the help

Closed 2018-05-26.

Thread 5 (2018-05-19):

Extruder cover - print needs supports

albegouws, 2018-05-19:
This bit needs supports or maybe rethinked angle here:

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

gregsaun, 2018-05-20:
If you check the STL there is a small support that comes with the part, you need to break it after the print.

In Fusion 360, if you check the bodies of this part you will see that their is two, one is hidden for "esthetic" but I unhidden it when generating the STL

Closed 2018-05-20.

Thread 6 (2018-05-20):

Feedback - Build completed

albegouws, 2018-05-20:
Just completed the build.  I reset the firmware to defaults and went through the whole self check again.  Calibration completed fine.

Build notes - X axis belts are 100% parallel now.  Distance between top and bottom of belts only differ by less than 1mm on 4 spots the whole length of the axis. X axis tension adjustment works perfect.

Inexperienced users should not attempt without proper instructions though.

X - carriage install was ok - however with no cable ties the install was a tad difficult especially when routing cables due to the weight of the extruder motor. On that - cable routing improved over original.  Filament sensor works ok so far, adjusting the tension on the bondtech easier with one screw too.  Unloading of filament seems easier with less of an blob than I had on the old setup.  Anecdotal for now, will tell you if that changes.

As a note I added this : https://www.thingiverse.com/thing:2904281.  It works ok-ish although the design can be improved to sit better in the v-slot and adjusting from the bottom is not really easy.  Can do with refinement, will see if I can improve on it when I can steal some time.

albegouws, 2018-06-01:
Hi - thought I'd ask here instead of opening a new issue.  Simple question - on the updates you note improved print quality and selective infill.  Would you mind explaining what that means ?  Not sure I get it.
Thanks!

zbrozek, 2018-07-03:
Just built one up. More feedback:

- The zip tie slots on the tail don't have an immediately obvious direction for retaining the upper harness vs lower harness.
- The x-carriage is super hard to install, especially during attaching the belts.
- Belt retention teeth are a bit tight. Maybe because I didn't print with linear advance.
- There doesn't appear to be any place for the nylon wire strain relief...?
- Would be nice to have a printed M10 thread in the sensor cover to accept a pneumatic fitting.
- Oh man the built in x-tensioner is so nice.
- Would be nice if you included a nozzle fan in the archive. I forgot to make one. Oops.
- Near the Rambo mount (on full Bear MK2.5) the harness tail gets *really* close to the case.

trevjonez, 2018-10-09:
Put this on my mk3 sans any bear frame. working great thus far. I didn't even add the x rod adjustment screws everything just felt great without. good work on the filament sensor cable port. my oem parts didn't retain the cable at all. yours fit like a glove. I assembled with a fresh hotend and your whole filament path appears perfect. I could see the .4 nozzle opening straight through the fully assembled extruder.

one thing that would make assembly a bit easier is if you could open up the gap on the bottom half of the x carriage back so that the inevitable on/off cycles are a bit easier to do. It works as is. but there is no wiggle to it. might be inexperience with the part but seems it could be 2mm or so wider without any strength issues.

when you rework the instructions make sure you put a warning on the x tensioner screw length. anything over 18mm will damage the part. I tried a 20mm and pushed in the wall a bit before I realized what was happening. part still working fine but something to look out for.

then on the x idler rod. I ordered a 3mm rod and cut it to length. but my pulleys were made based on the major diam of an m3 screw so really I needed like a 2.95mm rod. at that point I just said _**screw**_ it and grabbed my dremel and cut the head off a screw and used that. so far all is well. might be worth pointing out that a 3mm bore pulley on amazon might not actually accept a 3mm rod. more of a user experience thing than an issue with your design.

I installed this with the JLTX fixed z mounts at the same time. these x ends plus those z ends are the perfect setup for the stock mk3 frame. far more rigid, and the opening on the z makes install much easier.

next for me is to add the JLTX indirect sensor mod. looks like the hole pattern on the stock cover match yours so I am hoping his interposer is a bolt on fit. I might open up the fusion file and see if I can integrate his mod directly into your extruder body. lower part count would be a plus IMO.

also not sure if possible but it would be rad to replicate the adjustable pinda mount concept from the skelestruder.

all in all great work. this is more proof to me that scad workflow, while seeming cool is a nail in the foot of any decent designer/engineer. three production revisions from prusa and your alpha extruder is better IMO. key difference seems to be the design workflow making experimentation much simpler, but I speculate.

gregsaun, 2018-10-12:
@trevjonez Thanks you very much for this detailed feedback, very useful!

> one thing that would make assembly a bit easier is if you could open up the gap on the bottom half of the x carriage back so that the inevitable on/off cycles are a bit easier to do. It works as is. but there is no wiggle to it. might be inexperience with the part but seems it could be 2mm or so wider without any strength issues.

Are you talking about this opening in green?
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

> when you rework the instructions make sure you put a warning on the x tensioner screw length. anything over 18mm will damage the part. I tried a 20mm and pushed in the wall a bit before I realized what was happening. part still working fine but something to look out for.

It is true that 20mm and 18mm screws are very close and mistake can be easy. As my extruder will no use 20mm screws I will put a warning on the beginning of the assembly instruction

> then on the x idler rod. I ordered a 3mm rod and cut it to length. but my pulleys were made based on the major diam of an m3 screw so really I needed like a 2.95mm rod. at that point I just said screw it and grabbed my dremel and cut the head off a screw and used that. so far all is well. might be worth pointing out that a 3mm bore pulley on amazon might not actually accept a 3mm rod. more of a user experience thing than an issue with your design.

I know this is difficult to find proper size. I have improved description, hopefully it is good now. I am also planning to sell a hardware kit for the extruder with everything included to help people finding the hardware.

> I installed this with the JLTX fixed z mounts at the same time. these x ends plus those z ends are the perfect setup for the stock mk3 frame. far more rigid, and the opening on the z makes install much easier.

JLTX did a remix of my mounts in fact :-D

> next for me is to add the JLTX indirect sensor mod. looks like the hole pattern on the stock cover match yours so I am hoping his interposer is a bolt on fit. I might open up the fusion file and see if I can integrate his mod directly into your extruder body. lower part count would be a plus IMO.

This is a very nice mod from JLTX! Please keep me in touch with this, I am very very interested. I will not do this on final version because I want to avoid firmware update. However, this could be added in optional parts for advanced users

> also not sure if possible but it would be rad to replicate the adjustable pinda mount concept from the skelestruder.

I do understand and the way JLTX did it is very clever. However, I prefer to keep it simple and light as it is today. You do not need huge precision here and you are not touching it very often (for most people almost never).
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
matthew-humphrey, 2018-10-12:
@gregsaun why would the jltx indirect sensor mod require a firmware update? My understanding is he's just contacting the filament with a bearing and the sensor is reading the presence of a bearing rather than the filament (so the bearing is proxying the filament presence). This is just a mechanical change, no firmware change needed.

trevjonez, 2018-10-13:
> @gregsaun why would the jltx indirect sensor mod require a firmware update? My understanding is he's just contacting the filament with a bearing and the sensor is reading the presence of a bearing rather than the filament (so the bearing is proxying the filament presence). This is just a mechanical change, no firmware change needed.
>
> EDIT: Maybe firmware update because with the interposer there is an additional length of filament from detection before the filament is truly out?

The filament moving down spins a bearing. the sensor observes the other side of the bearing which is then moving up. The sensor is an IR laser that reports velocity and direction. the firmware mod required is simply changing a += operation to a -= operation so that the rest of the system still observes downward filament motion as down, etc.

gregsaun, 2018-10-14:
@trevjonez perfect explanation trevjonez, thanks!

>That is exactly the area that might use a bit more tolerance. so long as it doesn't harm function of course.
Ok I'll check if I can do something, it might sound that it will not perfectly hold the bearing... I am personally moving the spiral wrap a bit on the back, not the most safe method however...

@matthew-humphrey or rotate the filament sensor but hard to wire then :grin:

Pathogenius, 2018-10-26:
I've upgraded just the Z/X holders, and I must say this design is brilliant. I now have my X tension set perfectly. I love the visual instruction images, I hate reading endless steps and do prefer to figure stuff out via deduction. Beautiful!

QUESTION: What are those X-idler rod end screws for, maybe to push the rods out of the holder part. This would be one text note for the instructions that might be valuable. Anyways I just screwed them in all the way.

Now I wonder if there might be a Y-axis adjuster similar to this at some point? I managed to get my X into the sweet spot (255-270), and sure would love to get the Y the same, with such ease of adjusting that this solution provides.

gregsaun, 2018-11-18:
@Pathogenius I am going to explain this better in the final assembly guide. If you are on the FB group or Discord server "The 602 Wasteland" then you should find the article explaining it ;-)

Y axis adjustment is planed ;-)

trevjonez, 2018-11-27:
No sweat I already have an adjusted part on hand. just wanted to make sure you knew about it and there is a paper trail for the next person to search. trying to measure my belt it is .9mm and ~1.62mm total which leaves .72 ish for the tooth which is pretty close to what I can find on the spec for a gt3 belt. basically all I did is leave the teethe as they were and pushed the top side up .25mm. its a bit tight and I will need to sand at it to get it in. should have done .3 higher on the part I printed.

as I was looking at your carriage file it looked like there might be some tooth spacing issues as it goes around the bends. perhaps you can lock the pitch line as the ref point and then just do a pattern of whatever tooth profile along a path such that the spacing will auto solve? seems like the whole thing is a bit overly complex constraint wise so a single path with a tooth profile might be easier to deal with. I've not done that in fusion but it seems possible. will play with the concept if I can find the time. at least as a learning exercise for myself :)

gregsaun, 2018-11-28:
wow +0.25mm and still a bit tight, that is a really thick belt!

Part of the teeth are made with pattern but Fusion was not solving the angles correctly to me when doing it in a sketch. I tried to do it out of the sketch and was working better but the mirroring I am using to the other side did not work or was too boring to do. But now you give me another idea I can try :-)

trevjonez, 2018-11-28:
just to circle back the .25 adjustment was perfect once I cleaned up the part with a .8mm drill bit for the tooth grooves and an xacto blade on the flat side to remove any ooze drips etc...

Closed 2019-04-04.

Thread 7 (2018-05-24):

PINDA mount is 1.5mm too close to X smooth rods

gregsaun, 2018-05-24:
Because the X carriage is thinner by 1.5mm, the PINDA is closer to X smooth rods by the same dimension.

Panayiotis-git, 2018-05-24:
My measurements are not perfect (design imported to Tinkercad...), but related to the original design, I measure:
- In your design, the hot-end has moved closer to the X-axis rods by 2.2mm
- The PINDA has moved closer to the X-axis rods by 2.15mm

gregsaun, 2018-05-25:
Hi Panayiotis, thanks for helping me on this. Unfortunately, I have something quite different from my measurements :

X-Carriage MK2.5 from Prusa (STL imported) :
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

X-Carriage MK2.5 from Bear :
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

Pinda mount from Prusa (STL converted by [jzkmath](https://github.com/jzkmath/Original-Prusa-i3/)) :
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

Pinda mount from Bear :
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

So 1.5mm delta on X carriage, which means the Pinda mount should move by the same dimension

I will publish soon a fix with a better mount that helps for adjustment as well as maintenance and building.

Panayiotis-git, 2018-05-25:
Ok, you are right about the distances. You are talking about differences with MK2.5 and I measure differences with MK3.

But, I think the difference comes from the X-carriage thickness.
MK3: 15mm (12mm from edge to the center of the rod)
MK2.5: 14mm (11mm from edge to the center of the rod)
Bear: 13.5mm (9.5mm from edge to the center of the rod)

So, the 1.5mm you measure is 11mm - 9.5mm.

gregsaun, 2018-06-07:
Fixed in https://github.com/gregsaun/bear_extruder_and_x_axis/commit/f53affef560640b3b3778b92ea220dfee2910335

Closed 2018-06-07.

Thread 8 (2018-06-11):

F360 source file are outdated

Panayiotis-git, 2018-06-11:
Hi Grégoire,

do you plan to push the latest F360 files soon?

gregsaun, 2018-06-14:
Yes sure, sorry for this. I have a shroud that I do not like yet in the source files and to avoid problem I prefer to wait until I get something good. But this shroud takes much more work than necessary. Next week should be good with interesting new features as well!

Panayiotis-git, 2018-06-14:
Nice! I'm building a MK3 printer and I decided to use your x-axis and extruder design. I needed the source files to make same changes to the parts.
Anyway, since I am impatient, I printed your original parts.
The quality of your designs is superb!
All the bolts and nuts fit perfectly. I didn't use a drill, not even to a single hole.

gregsaun, 2018-08-06:
https://github.com/gregsaun/bear_extruder_and_x_axis/commit/dd3854dc0b37040ee7a7afbaa5813d2e0482567c

Closed 2018-08-06.

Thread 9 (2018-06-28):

X carriage back hits z-top

Panayiotis-git, 2018-06-28:
If the extruder is at the left-most or right-most positions and I increase the Z position, the x_carriage_back part hits the z-top parts.
And also, the filament spool holder, if z-axis moved to top.

gregsaun, 2018-06-29:
Sorry for my late answer, could you show me a quick and dirty photo where it is touching exactly?

Panayiotis-git, 2018-07-01:
Hi, sorry for the delayed answer, but I was not near the printer.

I have marked the problem area with a red circle. I'll try to take a photo, but it is a difficult shot.
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

Panayiotis-git, 2018-07-01:
Ok, I managed to get the photos.

1st and 2nd are for the z tops.
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

3rd is for the filament spool holder. In fact the holder touches the screw and the hits the orange plastic.
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

gregsaun, 2018-08-06:
Solved with new version published yesterday, thanks again @Panayiotis-git

Closed 2018-08-06.

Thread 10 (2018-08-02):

Improve stiffness for everyone and accuracy for Igus users with clamped bearing holders

zbrozek, 2018-08-02:
I was manually torquing my extruder a little bit to see what the least-stiff part of the assembly was. Turned out it was the bearing mounts in the X ends.

For Igus users, the bushings themselves aren't very stiff and they depend on the shell into which they are installed for stiffness. For all users, torquing the extruder will open up the bearing bore a little bit and allow the whole X axis to twist a little.

For reference, [these clamps](https://www.thingiverse.com/thing:2964026) seem pretty nice.

gregsaun, 2018-08-02:
Hi Sasha, thank you for the report. This is something I want to explore as well (plus other places where flex is coming). Good point for the Igus bearings. However, I do not recommend to use Igus bearing, specially on Z axis, they will add too much slop and this is not where the noise is coming from.

I have already updated the design of this part recently (but still no clamp yet) as well as print settings. Could you give me material and print settings you used?

zbrozek, 2018-08-02:
Oh, I'm using the Igus linear bearings because it's what I had on hand when my bearings failed. I had some spares on hand from an earlier attempt to quiet my Y axis. Regardless, the clamps are a nice touch to ensure that the shells can't be torqued open even with ball bearings.

I printed the X ends with 4 perimeters and 30% gyroid infill out of eSun ABS+. My next printer overhaul will make all plastic parts out of some flavor of PC.

gregsaun, 2018-09-20:
This is fixed with clamps on x ends (dev branch for now)

Closed 2018-09-20.

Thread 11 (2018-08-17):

Prusa R3 (extruder flow and cooling fan modification) vs. Bear Extruder

cskozlowski, 2018-08-17:
Any plan to improve extruder flow and move the cooling fan to a 45 degree angle similar to the Prusa R3 parts that were released in July, 2018?  It appears that Prusa put a good deal of thought into the new design, would any of this make sense for the Bear Extruder design?

Panayiotis-git, 2018-08-19:
The bearing of the fan wear out really fast when the fins are placed at the bottom. I've seen this happening many times.

gregsaun, 2018-08-19:
@Panayiotis-git reversing the fan is something I was thinking to avoid getting are too close to heated bed / printed part. Maybe it could help...

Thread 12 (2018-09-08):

bear_extruder_and_x_axis/printed_parts/stl/common/extruder_body.stl needs a 4mm brim

MikeRatcliffe, 2018-09-08:
Not a true issue but the following part needs a 4mm brim to print:

`bear_extruder_and_x_axis/printed_parts/stl/common/extruder_body.stl`

Otherwise the bit indicated in the picture has a tendency to fall over during printing.

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

gregsaun, 2018-09-20:
Next release will use a zip tie, like this you can replace pinda or nozzle fan without disassembling the body :-)

Closed 2018-09-20.

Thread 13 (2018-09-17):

Part fan shroud missing from 2.5 build

MikeRatcliffe, 2018-09-17:
The 2.5 build angles the part fan at 45<sup>o</sup> so the fan shroud cannot be used on bear builds, where the part fan lies parallel to the extruder.

Sadly, no fan shroud has been included in `printable parts`.

MikeRatcliffe, 2018-09-18:
The stock one can be used... closing.

Closed 2018-09-18.

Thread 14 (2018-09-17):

X-Carriage rod holes do not line up

MikeRatcliffe, 2018-09-17:
Note that this was not fixed by commit 21bc1fd85a458e9ea51c5ea404bc7ce8f9eb3d0b

Parts:
- x_carriage_back.stl
- x_carriage.stl

It is obvious from the image that the X-Carriage rod holes do not line up... well, they do but the shells don't.

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

gregsaun, 2018-09-20:
This took me some time to understand what was going on here but it is due to the fact that the thickness of the x carriage back is not the same everywhere (on purpose). A correct measurement shows that everything is correctly aligned :
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

Closed 2018-09-23.

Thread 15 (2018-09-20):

Use pancake stepper motor for extruder.

Graloth, 2018-09-20:
This is just a suggestion, but from the [Skelestruder](https://www.thingiverse.com/thing:2845416) I tested, it seems that using a much lighter slimline motor, doesn't give any negative effects in print quality, and can reduce the weight of the body by quite a bit (https://e3d-online.com/nema17-slimline-stepper-motor). From my testing you'd only need to run a single command (M92 E840) to update the printer to work with a higher resolution motor.

Once I can find some time, I'd like to test this out, initially by just using a slimline motor on your extruder body and see how it fairs, might even be able to move the motor even close to the rods since it weighs less and might not need as much supporting material to sit against.

matthew-humphrey, 2018-09-20:
Skelestruder has a reduction due to the pulley (6:1 I think) which gives it a significant mechanical advantage (more torque from same motor). Using the smaller motor on a 1:1 geared system like Prusa i3 and Bear will not give good results. Just look at all the posts on various forums about people having extruder skipping issues. And if you wanted to try it anyway, what prevents you from swapping the motor with the current design?

I do think that a system like Skelestruder is a great idea. In general I would trade speed for more torque on the extruder motor. But that's a separate issue, unless you are also suggesting that Gregoire add the gear reduction.

gregsaun, 2018-09-20:
Hi Graloth, and thanks for suggesting me this. My objective with the current extruder is to propose an easy upgrade to the stock one without changing too much the hardware and so keeping cost very low. As explained by Matthew you will need to use a reduction and this means we are going away of my objective.

However, I really think we can push this type of frame and axis much more. This will come in a different project based on the bear frame. But some configuration need drastic update and the extruder is only a part of the equation. So more to come but this will take a bit of time (as you might know, I like to take my time to design something good).

Closed 2018-09-23.

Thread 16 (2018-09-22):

Assembly guide specifies 20T toothed idler but BOM specifies 16T toothed idler

matthew-humphrey, 2018-09-22:
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

gregsaun, 2018-09-22:
20T idler is not released yet, only available in dev branch. But will be released tomorrow if everything is going well ;-)

matthew-humphrey, 2018-09-22:
Yes, I know, I am working off the dev branch and just wanted to make sure you saw this typo.

Closed 2018-09-22.

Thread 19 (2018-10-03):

Try to find a way to not have the shroud's hex nut falling down

gregsaun, 2018-10-03:
Might be hard to find the best compromise between easy installation and avoiding the nut to fall down

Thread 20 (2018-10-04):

Possible part cooling design?

trevjonez, 2018-10-04:
Looks like you are slated to do a part cooling shroud.

Might I suggest this design as an option? https://www.thingiverse.com/thing:3063554

it will keep the fan vertical thus not having an issue with the wear and tear that the r3 angle might induce. And the design seems to be decently tested for performance already.

I loaded it up and compared with the mk3 parts and it looks like shifting the fan and shroud forward about 1.6-2mm gives it adequate clearance around the pinda.(2mm shown in image)

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

robrps, 2018-10-04:
That's mine :) I do plan on doing a Bear version once I've assembled the 0.5alpha to see what's what. I'm quite slow thanks to my 7 mouth old daughter though... Mostly done in Fusion if anyone want the file.

gregsaun, 2018-10-04:
Oh nice to have you here! Happy you are interested in my Bear extruder :-) . I would appreciate to have the F360 file to adapt he place for the PINDA, would you prefer to send me this in private? Be sure that if I use your shroud (or a remix of it) I will add appropriate credits and license!

robrps, 2018-10-04:
I've had your Full Bear on my MK3 since RatRigs first sold the kit its a great design 👍 I'll message you on Thingiverse later on today with the file.

gregsaun, 2018-10-04:
Wow impressive Rob. Hope you like it :-) . Got your message thanks!

trevjonez, 2018-10-09:
I used three washers that are ~0.5..0.55mm thick per fan screw to get everything on nice and go figure it looks just like the above image. Been too lazy to draw up a fan shaped shim to print out as I figure even that would hopefully be a temporary solution.

matthew-humphrey, 2018-10-19:
I've been trying this nozzle out as well. I tried it both with no spacer washers, and with 3 spacer washers each on the two print fan mounting screws and the nozzle mounting screws. So far my results have been a bit better than with the stock Prusa R2 nozzle. I also did the water dish test, and I can see it's creating a circular indentation in the water around the nozzle.

matthew-humphrey, 2018-10-19:
I designed a spacer. I'll post a link once I have a chance to print it and test it out.

robrps, 2018-10-19:
If you are interesting trying out a Bear Extruder (v0.5a) specific version, then you can - https://www.dropbox.com/s/poudc3owi7r05y9/Initial%20Bear%20duct.zip?dl=0 It's not finished yet, but it's working as intended.

ufoDziner, 2018-10-20:
@robrps I'm currently using your duct on my 3 Bear extruders with great success.  Super excited to try out the Bear specific version.  I'll see if I can get them printing tomorrow.

I would really like the F360 files when you have it complete.  Thanks!

trevjonez, 2018-10-20:
I finally made a shim yesterday. it is a quick and dirty copy face from the front of the extruder body. but works. honestly I was considering doing something similar in tpu just so I could see if it quites the fan down.
[bear fan shim.stl.txt](https://github.com/gregsaun/bear_extruder_and_x_axis/files/2498203/bear.fan.shim.stl.txt)
 rename without txt before using

matthew-humphrey, 2018-10-27:
Interesting, here is the shim that I made.
[Spacer.stl.txt](https://github.com/gregsaun/bear_extruder_and_x_axis/files/2521465/Spacer.stl.txt)

matthew-humphrey, 2018-10-27:
Interesting. This is the spacer that I made.
[Spacer.stl.txt](https://github.com/gregsaun/bear_extruder_and_x_axis/files/2521468/Spacer.stl.txt)

@robrps - I tried this latest version and it is not even remotely close to fitting on my extruder. @ufoDziner are you using his version from the dropbox share, or the one that was posted to Thingiverse?

Pathogenius, 2018-10-27:
I'll just forward this little known remix of the R3 shroud, which, if you look closely, you can see the air has less of a fight to get through, and also, less air is allowed out the first exit holes, and is redistributed deeper.

https://www.thingiverse.com/thing:3078174

matthew-humphrey, 2018-10-27:
I don't like the R3 fan position. With those cheap fans, it's going to cause premature bearing wear and eventual fan failure. What I like about @robrps design is that it works great with the original fan position (assuming  you use the spacer, or some washers). I'd really like to see an update of it that doesn't require the spacer.

matthew-humphrey, 2018-10-27:
Here's a version with the Bear logo cutout to save a little plastic (good idea, @trevjonez )
[Spacer.zip](https://github.com/gregsaun/bear_extruder_and_x_axis/files/2521477/Spacer.zip)

robrps, 2018-10-27:
Yeah, my bear duct is a little too tight at the moment - it doesn’t require screws to hold it in place! It also blows a little too much on the block, so without a sock it can cause issues. I’m starting that design again but parametrically so adjustments can be made using parameters. Just getting to grips with Fusion360’s way of doing things. I’m more used to NX but I want others to be able to make changes.

matthew-humphrey, 2018-10-27:
@robrps, It looked like the issue was the mount hole was lowered too much. I'm using your previous design with my spacer now and it's working well. BTW, @gregsaun has been making some changes to the extruder in the dev branch, mostly to improve hotend cooling, so you may want to check to make sure there aren't any fitment issues with the new design.

ufoDziner, 2018-10-27:
@matthew-humphrey I'm using the dropbox version.  It is very close tolerance as @robrps stated, but seems to be working okay.  I mount the shroud to the extruder first, then add the fan after.  Make fitting it much easier.

ufoDziner, 2018-10-28:
@matthew-humphrey Just in case you didn't notice this; part of this shroud goes on the inside of the extruder cover.  It's not like other shrouds.  The inner flange goes inside, then the screw mounting flange goes on the other side of the wall.

matthew-humphrey, 2018-10-28:
@ufoDziner - Yes, that was exactly the issue. Thanks again.

robrps, 2018-10-29:
I've done an update to my bear cooling duct. If you are feeling brave, you can download from the links below. I've finished it during my lunch break at work (Shhhhhhh!!) so I've not been able to print or test as yet. There are 2 version, one similar to the last, the other has a staggered exits at the side.... might be worse! Print with 3 perimeters and a print width of 0.45.

https://www.dropbox.com/s/u23mmxfw3rlxaw5/Bear%20Part%20Cooling%20-%20Non-Staggered.stl?dl=0
and
https://www.dropbox.com/s/2a102sx6pk2locn/Bear%20Part%20Cooling%20-%20Staggered.stl?dl=0

If I can get the Fusion exporting working I'll link the file. But it's a distributed design so its not letting me. but the angle, exit width, stagger and wall thickness are all adjustable parameters.

trevjonez, 2018-10-29:
I just got the first bear one on and fit and function has been great. I'll give these a spin. only thing I wonder is if we can do anything more to have the air flow angled more downward towards the part/bed?

matthew-humphrey, 2018-10-29:
@robrps - @gregsaun shared with me a technique to get the Fusion 360 export working when it gives you that error about the distributed design. From Gregoire:
1. Within Fusion 360, click on top of your project (note _project_, not design - this is in the pane on the left hand side of the screen, at the very top). This will open the project in a web browser.
2. Navigate to your model, and then click the Export icon.
3. Choose the F360 format.
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
RH-Dreambox, 2018-12-28:
Here comes another air nozzle for vertical fan mounting. It is a prototype with only two exhaust ducts and the aim was to create as small a nozzle as possible. Gregsaun wanted as small a footprint as possible down to the bed.
The nozzle is designed for Bear extruder, but it also fits the standard MK3 with vertically mounted cooling fan.

The difficulty with a small nozzle is to direct the airflow to a particular point. I do not know if I will go any further with this model, but please try it and say what you think. If it does not perform well, I may try another model.

Parts of the nozzle are very close to hotend, so it may not be suitable for large prints in ABS. See it as a test, it's a prototype. I try to find out what causes heat problems with the left side of the nozzle. When we know that, we should be able to fix that problem on the extruder.

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
[Nozzle_Bear_RHD_Rev.0.zip](https://github.com/gregsaun/bear_extruder_and_x_axis/files/2714970/Nozzle_Bear_RHD_Rev.0.zip)

robrps, 2018-12-28:
Nice, I like how you've used the space under the inlet ramp and of course the simulation results. You do have a couple of 90° degree bridges happening at the inlet though, but it looks like you have enough room to add a supporting angle under those to help print-ability.

I'll print it and test it on my overhang model that I posted further up.

RH-Dreambox, 2018-12-28:
No support material is needed. I have printed it in ABS and it was perfect. Please use my attached gcode.

robrps, 2018-12-28:
It printed fine. I printed my overhang test with yours and again with my current one above (3 exits). There is no discernible difference between them. I would say yours performs better than my duct when it only has the two side exits. Have you experimented with a forward facing exit as well?

My overhang test has 4 compass point overhangs with 48.4°, 66°, 73.5° and 77.5° (or 0.5, 1, 1.5 and 2 perimeter) overhangs - assuming 0.2 layer and 0.45 extrusion width.

I'll post photos tomorrow.

matthew-humphrey, 2018-12-29:
I loaded your config into Slic3r from the g-code, and printed the nozzle. It appears that you have thin walls enabled and this is causing an issue in my version of Slic3r PE (1.41.1). Specifically, the "Bear" text on the back is breaking through the wall, creating an undesirable path for the air to take. Disabling "Detect thin walls" resolves the issue.

robrps, 2018-12-29:
@RH-Dreambox Photos attach. Speeds 30mm/s bridges, 75mm/s perimeters. 0.2mm layer and 0.45mm line widths. I am running Klipper firmware at the moment.

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

In your simulation software, have you positioned anything just below the nozzle to simulate what and where the blown air goes during a print? Like a flat plane, or a horizontal or vertical wall?

robrps, 2018-12-29:
I've uploaded my Bear duct to Thingiverse - https://www.thingiverse.com/thing:3320490

The only change to the beta 5 a few posts up is I've added a tear drop to the mounting screw hole.

gregsaun, 2018-12-29:
@RH-Dreambox do you think you could reduce the green distance on this picture?
@robrps I would ask the same question for your nozzle

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

Reducing this section is important because it will cover less the printed part and will then allow better cooling of latest layer

RH-Dreambox, 2018-12-29:
> In your simulation software, have you positioned anything just below the nozzle to simulate what and where the blown air goes during a print? Like a flat plane, or a horizontal or vertical wall?

robrps, 2018-12-29:
https://a360.co/2Tkoqo7 - Overhang test part in Fusion. Modify -> Change parameters to adjust.

@gregsaun Surely that distance is needed for the fan duct to sit in?

RH-Dreambox, 2018-12-29:
Gregsaun, you ask for the impossible!
But I will bring out my magic wand and see what it can do :-)

matthew-humphrey, 2018-12-29:
@robrps that overhang test  object is fantastic. Thanks for sharing.

RH-Dreambox, 2018-12-29:
> I loaded your config into Slic3r from the g-code, and printed the nozzle. It appears that you have thin walls enabled and this is causing an issue in my version of Slic3r PE (1.41.1). Specifically, the "Bear" text on the back is breaking through the wall, creating an undesirable path for the air to take. Disabling "Detect thin walls" resolves the issue.

Thanks for the tip, I tested and it worked. I just don't understand how I've done before ???

matthew-humphrey, 2018-12-29:
@RH-Dreambox
> Thanks for the tip, I tested and it
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

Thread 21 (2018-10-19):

Unable to remove filament from bowden cover when filament sensor kick it because it is the end of the filament

gregsaun, 2018-10-19:
Filament sensor needs to be disassembled.

https://www.facebook.com/groups/prusabearupgrade/permalink/1105132772980365/

trevjonez, 2018-10-20:
so can I tag on another chore to this one? the sensor cover screw arrangement is just slightly different than the stock arrangement. as I was trying out the JLTX interposer yesterday I could only use one screw to attach it and still have the filament path line up.

gregsaun, 2018-11-18:
@trevjonez screw are going to be totally different on the next version unfortunately

gregsaun, 2018-11-19:
fixed in release 0.6.0-alpha

Closed 2018-11-19.

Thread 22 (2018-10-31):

Quick assembly image is showing GT2 instead of 2GT

GurliGebis, 2018-10-31:
Like the title says, the quick guide image needs to be updated :)

gregsaun, 2018-11-19:
fixed in release 0.6.0-alpha

Closed 2018-11-19.

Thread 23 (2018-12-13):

MK2(s) compatibility state?

BenRoe, 2018-12-13:
Hello,
i did the bear upgrade and updated my MK2S to MK2.5.
Now i build a MK2S with the left frame/parts.
Can i use this extrude/x-axis parts for a MK2S build (without filament sensor and old pinda)?

mattiras, 2020-03-10:
Hi @BenRoe

Are you still building Bear MK2? It is possible to get Bear X-axis work on MK2. I have modified the probe offset on 2.3.2 firmware and It works without issues.

https://github.com/mattiras/Prusa-MK2-Firmware-for-bear-x-axis

If you like. Try it to confim. (at your own risk). Are you able to compile?

gregsaun, 2020-03-10:
@mattiras Nice!

Closed 2019-01-11.

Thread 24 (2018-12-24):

Misplaced air-nozzle mounting holes

RH-Dreambox, 2018-12-24:
Hi Gregsaun,
I work with a new air-nozzle that will fit your extruder.
But when I assemble the extruder I see that some holes need to be moved, this in order to maintain full compatibility with the original extruder.

At the attached drawing you will see what needs to be done. In addition, I would like a little support for the right side of the air nozzle (see drawing).

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

gregsaun, 2019-04-04:
I close this one as we are going to tackle this wit the #20 issue .

Closed 2019-04-04.

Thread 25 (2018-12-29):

Bondtech tightner (single) misaligned

TurboMech, 2018-12-29:
@gregsaun I've been running this setup for a while before the public release and now the bondtech gears are slipping on the filament.  I believe this is due to the hole (for the tightener) being placed over the gear's meshing teeth and not closer to the teeth for the filament.  This is causing the filament to extrude sometime and not extruder other times.

Although this could be due to body parts warping when printing at high temperatures within my enclosure.

TurboMech, 2018-12-29:
@gregsaun I'm not quite where the issue lies or if you fixed it in the latest revision.  But it seems if the idler door warps even slightly then it will not allow the bontech gears to be close enough to grab filament.  I need some more time to work on this, but I think if the tensioning screw was aligned where the filament teeth are on the bondtech gears I think it may work better and allow for more or less tension on the filament

gregsaun, 2019-03-13:
@TurboMech  sorry for my late answer. It is possible that the Bondtech teeth (big ones) are not meshed together correctly and so the door does not close well. Is it what you are talking about?

Closed 2019-04-04.

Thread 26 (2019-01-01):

x-carriage compatibility with new bondtech extruder

joeycerone, 2019-01-01:
Hi Greg,
Wondering if the current x-carriage and x-end parts are compatible with the newly released bondtech extruder upgrade for the mk3? I have one on order and was planning on upgrading to your parts if they are compatible. If not, do you plan on updating them in the near future? Thanks.

gregsaun, 2019-01-09:
Hi Joey, as you may probably know, the Bondtech carriage is available here :
https://github.com/gregsaun/bear_extruder_and_x_axis/tree/master/optional_parts/bondtech_x_carriage

Closed 2019-01-09.

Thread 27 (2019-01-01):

[Quick assembly] Z nut missing from part list ?

anthonyda, 2019-01-01:
Hello,
When looking at the instruction/manual, there doesn't seems to be any references to the black Z nut (where the threaded rods goes) that we can see here : https://github.com/gregsaun/bear_extruder_and_x_axis/blob/master/manual/quick_assembly.md

Can you please please edit the part list ( here : https://github.com/gregsaun/bear_extruder_and_x_axis/blob/master/manual/bom.md ) with the reference to this part ?

TY

photog0411, 2019-01-03:
It's the ones that come with the printer

anthonyda, 2019-01-03:
Sure but I've got a prusa clone and would like to adapt it to my printer.
So I'm looking for the part reference in order to buy it.

middelink, 2019-02-03:
I guess you want something like this:
https://www.aliexpress.com/item/2pcs-Original-Prusa-i3-MK2-MK2S-MK3-3d-printer-Z-axis-Trapezoid-Motor-Screw-Nuts-For/32860620795.html

nicpottier, 2019-06-04:
Anybody know how these compare to say standard brass ones in 2mm pitch, such as these?
  https://www.aliexpress.com/item/T8-Trapezoidal-Nuts-8mm-Part-Copper-Screws-For-Stepper-Motor-Lead-Screw-Diameter-10mm-Pitch-2mm/1000006527658.html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,searchweb201602_2,searchweb201603_52

nicpottier, 2019-06-04:
Or shorter: https://www.aliexpress.com/item/Geeetech-2pcs-lot-3D-Printer-Parts-M8-Copper-Nut-for-Diameter-8mm-Pitch-2mm-Z-Axis/32821734240.html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,searchweb201602_2,searchweb201603_52

gregsaun, 2019-06-15:
All datasheets will be available with the next release coming very soon.

In the mean time you can find them in the bom on the dev branch:
https://github.com/gregsaun/bear_extruder_and_x_axis/blob/dev/manual/bom.md

Closed 2019-06-15.

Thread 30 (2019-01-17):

Alternative to Sunon MF40100V1-1000U-G99

timwj2016, 2019-01-17:
The Sunon MF40100V1-1000U-G99 is recommended as an alternative to the Noctua fan however the Sunon seems very difficult to source.  Is there an alternative to the Sunon that has similar specs?

Thanks

Tim

timwj2016, 2019-01-17:
I am in the US and everyone, including DigiKey, seems to have the A99 but not the G99.  I ordered the Delta and will give it a try.
Thanks

mmarbut, 2019-01-18:
I got mine here out of stock for now though.
https://all3dmakers.com/products/sunon-mk2-5-mk3-5v-hotend-cooling-fan?variant=17134119780467

j00sef, 2019-01-30:
All3D Makers have the fan where you can splice it to your existing cable if you can't wait for the pre-assembled ready to go one.
[https://all3dmakers.com/products/sunon-mf40100v1-1000u-g99-hotend-cooling-fan](url)

matthew-humphrey, 2019-01-31:
I tested the Delta fan that I linked above. I have a temperature probe and PTFE tube assembly that I can use to sense the temperature in the critical region of the heatbreak. I ran some tests with hotend at 260C and extruder just above an 80C heatbed. With the Sunon V1, the temperature in this region of the heatbreak was 35.8C. With the Delta it was 36.5. With the Noctua, it was 40.9.

So although the Delta is not as good, it is very close. I found the noise levels similar to the Sunon V1.

And yes, All3d has the Sunon V1 now, so you can just go with that.

gregsaun, 2019-04-04:
I have added the Delta to the dev branch now. Thanks everyone for helping me on this topic and thank you again @matthew-humphrey for having find the Delta!

rrauenza, 2019-04-24:
I happened to be researching the different specs of the Noctua vs Sunon in order to upgrade my stock mk3’s extruder fan and came across this issue - so I thought I’d also document them here for others.

What I found surprising is the difference in static pressure between the Noctua and the Sunon - 1.78mmH2O vs 4.83mmH2O (0.9inchesH2O) - almost a 3x difference.  Volume is 8.2m^3/hour vs 13.6 (8 CFM).

Of course it is also has a higher rpm and is louder ... but reportedly helps with jamming.

https://noctua.at/en/nf-a4x10-5v/specification
http://www.sunon.com/uFiles/file/03_products/08-catalog%20download/Sunon%20DC%20Brushless%20Fan%20&%20Blower_(240-E).pdf

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

austinvojta, 2019-05-22:
How about this one from CUI? Looks like an exact match to the Sunon V1. Same CFM, SP, and noise level, all while also being 5V with tachometer signal:

CFM-4010V-070-273-20

https://www.cui.com/product/resource/cfm-40v.pdf

adudek16, 2020-05-17:
Octopart.com seems to be a good source to find who has stock.

tcurdt, 2020-07-13:
Just to clarify: The A99 is not an acceptable alternative to the G99?

Closed 2019-04-04.

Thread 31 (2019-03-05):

PINDA Mount STL ISSUE - Dev Version of MK2.5S/MK3S

micahvestal, 2019-03-05:
The PINDA probe mount on the new MK2.5S/MK3S STL is lower in Z space than the main extruder body, making it unprintable as arranged. I know it's just a Dev version but thought I would share my feedback.

gregsaun, 2019-04-04:
This is fix now, thanks for having reported it :-)

Closed 2019-04-04.

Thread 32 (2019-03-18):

Allow motor removal without tearing down extruder

guykuo, 2019-03-18:
I have been experimenting with 0.9 degree motors in x, y and extruder positions and having good success in all three positions.

https://shop.prusa3d.com/forum/user-mods-octoprint-enclosures-nozzles--f65/stepper-motor-upgrades-to-eliminate-vfa-s-vertical-t28098.html

One suggestion I have is to allow motor removal without needing to tear down the entire extruder. This can be achieved by...

1. Shifting lower left, rear cover bolt laterally.

2. Add access holes through mounting plate to reach motor bolts. These holes would go through the upper bearing mounts and ideally be large enough to fit M3 bolt head.

If these simple changes were made, motor swaps could be performed by removing the upper rear cover, slipping the upper bearings out of the way, and removing the four motor bolts. This would dramatically simplify swapping and servicing of the motor. The present design requires a much more extensive tear down to change motors.

My rough artwork below shows the suggested changes.

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

One of the big draws of the Bear extruder is easier service. This mod extends ease of service to the stepper motor.

guykuo, 2019-03-21:
Here are some STL's for the MK3 that implement the requested changes. Sorry for the rough editing. This is my first time using Fusion 360

[Kuo motor service Bear X Carriage Mk3.zip](https://github.com/gregsaun/bear_extruder_and_x_axis/files/2991110/Kuo.motor.service.Bear.X.Carriage.Mk3.zip)

guykuo, 2019-03-24:
Added holes to top rear carriage cover as well. Now you don't even need to remove the cover nor detach the filament sensor cable to undo lower motor bolts. Just reach in with wrench.

While I was at it, took care of another annoyance - dropping those little white washers when idler door is removed. I modified extruder body and idler door so they hinge independent of the motor. Printing the body with the mod requires a support. I have added a Slic3r 3mf file that has all the modified parts and support enforcer already in place.

Long bolt that used to be axle for idler door may optionally be cut and to engage nylock instead of motor.

Here I have removed the motor without removing printer from its enclosure. Just reached in from front of enclosure to do all the work. Fans, hot end, PINDA, filament sensor, and rear carriage covers were left in place during motor removal and replacement.

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

Here are updated STL's and 3mf file
[Kuo motor service Bear X Carriage Mk3 b3.zip](https://github.com/gregsaun/bear_extruder_and_x_axis/files/3000174/Kuo.motor.service.Bear.X.Carriage.Mk3.b3.zip)

gregsaun, 2019-04-04:
@guykuo sorry for my late answer, I try to take tasks one after the others :-D . Huge thanks to your research on motor, this was something I planned to do since a long time. I could not find time yet to read everything yet but for now your results are matching perfectly my feelings.

I did thought about this and I drop that idea. The carriage back with screws instead of zip ties is having quite a lot of torque and with screws not centered on the bearings you might twist it a little. This will probably not something that will be true for everyone but I prefer not to take the risk as those axis are very sensitive.

However, just thinking now, maybe we could give access to motor screws in diagonal and using a screw driver with a ball at the end. Do you think we have room for that?

Finally, you did a great job on the design too, congrats!

guykuo, 2019-04-04:
I understand your theoretical design concerns regarding bearing alignment, but I doubt they are a real life problem. Your x-carriage and cover are fairly stiff and conform tightly to the bearings. They just don't budge once bolted - even with moderate torque and my offset bolt placement. Your designed parts are definitely stiff enough to do the job well. I don't see any changes in x-axis effects on y-faces in my test prints before and after the bolt offsets.

How about symmetrically offsetting the cover bolts. I didn't try doing that I only had a few days of Fusion 360 experience. Symmetric offset combined with the stiffness and excellent conformity of your parts design should allay bearing deviation concerns.

Angled approach to the motor bolt heads might work, but it must remain under 20 degrees angle or some ball head wrenches won't engage. Also, the angle will worsen as bolt is backed out.
Another feature of straight through bolt access was useful during my 1:3.5 gearbox attachment testing. I needed to change bolts to slightly longer ones. Angled access hole have made bolt removal impossible without further extruder tear down.

gregsaun, 2019-04-05:
I will see if I can give a try with a slight angle to access the screw, I have few ideas.

Oh I did miss the gearbox thing, did you post it somewhere? That looks very interesting. Also, if you want custom motors and are searching something specific please let me know and I can check with LDO to help you. Cannot promise anything, but we can try.

guykuo, 2019-04-08:
Gearbox is now on Thingiverse

https://www.thingiverse.com/thing:3550304

I'm looking forward to your official updated design with screw access. Mine works nicely with the screws and independent idler door, but something official from you would be nice for others. I am refraining from publishing on Thingiverse as a remix, until you do your thing.

BTW, the gearbox + your extruder is pretty awesome. I have the Bondtech kit also in hand, but this is working very well and I retain fast access for experimentation. Going with the actual Bondtech upgrade, I would lose a lot of experimental flexibility but would gain just a little bit better performance.

gregsaun, 2019-05-28:
Hey sorry again for my last answer. I did some test and will not make the motor removal like you proposed. I could not find another solution that works for me so unfortunately this will not come from me.

Your gearbox is getting pretty famous at the moment, several people are using it, congrats! 😃

guykuo, 2019-06-10:
Yes, the BNBSX extruder has really taken off.

I'm surprised that your testing didn't work out, but based on your concerns regarding bearing stability, I'm adding another screw to the upper cover to maintain even force across both upper bearings.

gregsaun, 2019-06-10:
You made a great work with all your testing and design.

I have recently change the bearing pocket to make it less prone to over-tightening, have a look on the dev branch.

The problem with bearing is that it will work for most people but my community is quite big today and I have to be sure my parts work for everybody. For example, people are using Vesconite bearings, old/new Prusa rods, Misumi rods, all sort of chinsium bearings/rods, more professional bearings like IKO and so on. Some people have reported issues with Vesconite already, they were unable to use the 3 bearings on the X carriage.

Having a bearing that is not tightened with "equal force" might results in several issues like crash detection or premature wear of the rods/bearings. It might also generate artifacts in prints that are not always easy to understand or track.

guykuo, 2019-06-10:
That IS a wide variety of bearings and rods to support. No wonder you are so conservative in that respect. Meanwhile the bunnies just keep pushing buttons. Here is what your carriage has morphed into with five screws for the upper cover. With the new 5 screw configuration, the upper cover once more has uniform clamping force along length of both upper bearings.

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

Lower cover had to be reconfigured to become hot end safe for R4 height extruders. The original configuration was destroying my hot end cables during XYZ calibration. Also, the bottom edge was too close to heat block and melting when used with short R4 height extruders.

gregsaun, 2019-06-10:
I appreciate you are pushing boundaries and this is exactly why I do my project in open source!

This is better for sure, but you will might have some different flex in the cover with the hole on the right compare to the those on the left. Sorry, still not compliant to my design "rules", but does not mean I am correct :-D

Are you sure the filament sensor cables are not touching when the extruder is full up?

Have you seen that the MK2.5 version reduce print surface on X axis due to longer end stop arm (and cables centered on the back)?

Yes I know for the hotend cables, they fixed it differently now by moving the nut on the heated bed cable cover. I am not very fan of this because you might shortcut bed connection when using a wrench to tighten the nut between the two + and - screws.

guykuo, 2019-06-10:
Would not have been able to get so far without your files. They are barely recognizable now, but you created a fantastic base. It is amazing that the PINDA mount does not melt even with prolonged printing of polycarb. The only problem is screw gradually getting loose on PINDA clamp after a few hundred hours. I just changed PINDA mount to use Nylock instead of M3S to combat that issue.

I noticed the stop arm seemed a few mm longer, but wondered if I had inadvertently shortened mine. I'm not becoming feeble minded.

That rear cable routing also thickens the extruder assembly. Not great for moment arm.

Filament cables are fine. Their rearmost position still clears frame.

gregsaun, 2019-06-10:
Happy you like it and find it useful.

I kept the grid for that but as you mention it is still not totally safe. You can also add a dab of Loctite or reduce the hole diameter to have plastic art acting like a nylock. Pinda is also badly placed because it is very sensitive to temperature, they should really move it somewhere else.

I am really not a big fan of this smaller extruder height. Which is why I stick to older design for now.

Closed 2019-06-15.

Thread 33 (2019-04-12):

Integrated Bunny Science Gearbox into Bear Extruder

guykuo, 2019-04-12:
Now testing what would happen when combining Bear extruder with Bunny Science. Moves motor 14 mm closer to x-rods than gearbox bolt-on. That's even a few mm behind the front of the normal Bear extruder body.

https://www.thingiverse.com/thing:3560341

It works...
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

guykuo, 2019-05-14:
Pressed onward to MK3S sensor both standalone and MMU2s in my BNBSX variant

https://www.thingiverse.com/thing:3626993

Closed 2019-12-16.

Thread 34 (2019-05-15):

x_carriage_back.f3d file

gorillamotors, 2019-05-15:
I am building a Bondtech BMG-M Extruder / Mosquito magnum hotend to my Prusa MK3. I am also adding some Igus RJZM-01-08 bearings. The problem is that the bearings are 16mm x 25.25mm and the Bear parts are 15.3mm x 24mm and the bearings don't fit. Could you please attach the x_carriage_back.f3d file to this file so that I can modify the file.

gregsaun, 2019-06-15:
Hi, sorry for my late answer, the Fusion 360 sources are all available here:
https://github.com/gregsaun/bear_extruder_and_x_axis/tree/master/src

Or in optional part like for the Bondtech X carriage:
https://github.com/gregsaun/bear_extruder_and_x_axis/tree/master/optional_parts/bondtech_x_carriage

Closed 2019-06-15.

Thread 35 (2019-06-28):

BMG-M

bpvarsity, 2019-06-28:
Is there a way to mount the new BMG-M that was released for the slice mosquito with this setup?

gregsaun, 2019-06-30:
Are you talking about this one?
https://www.bondtech.se/en/product/bmg-m-extruder/

bpvarsity, 2019-06-30:
Yes

gregsaun, 2019-06-30:
I have not seen this being compatible with Prusa printers sorry, do you have a link?

bpvarsity, 2019-06-30:
Ah just heard from bontech they have one coming out for prusa soon. It's in beta testing so that will be be great. Should work and mount like the other BMG upgrade kit for prusa printers you support

Closed 2019-12-16.

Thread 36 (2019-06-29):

X-carriage rod holes too tight

haarp, 2019-06-29:
Hi,

I've printed the X-ends on an i3 MK3 out of PETG with the recommended settings: 0.20mm, 5 top/bottom, 4 perimeters. I only deviated by going with 40% infill instead of 20%. I am confident that my MK3 is as precise and well-tuned as it gets.

Unfortunately I'm having trouble inserting the smooth rods (Igus SWM-08). I'm leaning on the X-ends with all my weight and the rods still won't go all the way. I actually ended up having to hammer on the ends with a mallet. They scrape up a bit of material on their way. Of course this hurts precision... And I can forget about the "X smooth rods tension" or ever removing the rods again without breaking the ends.

Do you have an idea why this happens? I suspect that the lack of chamfer on the Igus rods might be the problem. Unfortunately I don't have any other rods to test.

gregsaun, 2019-06-30:
Hi Haarp,

The missing chamfer on the rods is probably not helping. Unfortunately, those rods are hardened steel so it will be hard to add a chamfer. You could try with a electrical grinder tool.

My holes have the same size and shape than original Prusa ones. They are a bit on the tight side because Prusa is using a reamer (or drill bit) to make the diameter more precise. You could try to use a 7.95mm reamer on the holes to make them more suitable to your rods.

Note that their is a small pocket at the end of the holes for the chips made during insertion of the rods.

trevjonez, 2019-06-30:
I always use an 8mm bit to ream them by hand, I do it by hand so that I don't accidentally over drill or crack the part. Most drill bits i've measured are slightly under the size they say so it should still come out a snug fit after using an 8mm bit.

vertigo235, 2019-06-30:
I always use the rod and chuck it into my drill and drill the rod into the ends at high speed. The heat generated from friction opens the pocket up just right.

haarp, 2019-07-01:
> Prusa is using a reamer (or drill bit) to make the diameter more precise.

Ah, that makes sense! I did not know that.

In other news, I've taken the plunge and tore apart my current Mk3 to assemble the Bear X axis. Tunrs out the Prusa rods go in much much better than the Igus ones. Still not a perfect fit in all holes, but at least I don't have to grab a mallet :)

They also slide better on the bearings. I guess the surface material and chamfer does make a ton of a difference. Guess I'll be sticking with the Prusa rods.

Thanks for your replies!

Closed 2019-07-01.

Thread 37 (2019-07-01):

MK3 version?

jokeane, 2019-07-01:
Hi, I see now with the latest version it only shows MK3S? Does this also work with a MK3?
I printed and built an earlier version and installed it on my MK3, and it works fine, but I'm curious about compatibility of this latest version of the parts. Thanks!

gregsaun, 2019-07-01:
Works totally fine except that you can't use the laser filament sensor. You can use the stock firmware as well with this one.

Closed 2019-07-06.

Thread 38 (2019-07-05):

M3x16 Button Head screws missing from BOM for Sunon Fan

harlanaubuchon, 2019-07-05:
Four M3x16 Button head screws are needed to complete the Sunon Fan assembly.

BOM:
https://github.com/gregsaun/bear_extruder_and_x_axis/blob/master/manual/bom.md

Assembly Guide:
https://guides.bear-lab.com/Guide/3.+Extruder/13?lang=en#s133

gregsaun, 2019-07-05:
It is explained under optional part -> hotend fan but I'll try to make that cleaner.
https://github.com/gregsaun/bear_extruder_and_x_axis/blob/master/optional_parts/hotend_fan/

harlanaubuchon, 2019-07-06:
Maybe I'm an outlier but, I ordered all new hardware from the BOM and a new hotend beforehand so I could assemble the vast majority of the upgrade without tearing down my printer.

I don't feel like this project should have to keep track of all the hardware for the optional upgrades but, this one in particular needs screws most people won't have and is not really optional for performance reasons.

I'm happy to contribute some markdown if you'd like a pull request.

gregsaun, 2019-07-06:
I made it clearer in both Bom and optional parts:
https://github.com/gregsaun/bear_extruder_and_x_axis/commit/62619b686c6ef510dce2515593c5fb3f0e496ed6

Thanks for reporting it.

Closed 2019-07-06.

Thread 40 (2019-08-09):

Parameterize trapezoidal nut size?

nicpottier, 2019-08-09:
Howdy howdy. I'm building a bear from scratch and using 8mm lead screws with a 2mm lead. I have two different kinds of trapezoidal nuts (one brass, one POM) and both have nuts 15mm apart instead of the 19mm that the stock Prusa nuts have.

No problem, I can change that in the fusion 360 models (yay!) and I can edit the literals in the sketch there to make it work, but what would you think about these being User Parameters?

Seems we could accomplish this with a single new parameter, the distance between the bolt holes in the nut. Everything else could be based on that.

Main benefit here is that as you continue to evolve then those of us using slightly different things can rebuild our STLs by just changing one parameter.

Happy to make these changes and submit a PR (does that work for fusion 360 files?) if you agree.

nicpottier, 2019-08-09:
So playing with this on my own looks like we would need one more variable as the hole size for the lead screw is actually a bit larger than just `trap_nut_hole_distance - m3_nut`

The above with 19 mm for `trap_nut_hole_distance` (stock prusa) has us come out to 12.9 instead of 13.5 per stock.

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

Is this slightly larger hole for reasons of being on even perimeters or something? Just wondering what the right way to model that would be.

nicpottier, 2019-08-09:
Hrmm.. devil is in the details I see, a lot more is dependent on those values than just that, all sorts of errors! Will keep playing with this but also investigate printing a 2mm lead nut with the same dimensions! :)

gregsaun, 2019-12-16:
Hello, sorry for my late answer, thank you for your interesting issue, I agree that it would be great. Have you found a solution for this?

nicpottier, 2019-12-16:
For the time being I ended up just using an adapter. Got a bit stalled on this build so haven't seen how it prints yet but will let you know when I get there!

ChipTechno, 2020-04-16:
I made a simple adapter for 22mm->25mm nuts. With this we can use the standard 22mm nut size on the X part https://github.com/ChipTechno/Bear-upgrade-snakeoil-mod/tree/master/Lead-screw-nut-adapter

trevjonez, 2020-04-16:
I have been running printed nuts on my machine for about a year. It is quite difficult to get good results.

I am going to give the adapter a try as I have just recently failed to print nuts in pom.

Currently my nuts are in essentium PA and while functional it has more friction than I want, thus need replacing far more frequently.

trevjonez, 2020-04-18:
I've given the adapters a go and love how they look and fit, but I don't like how constrained the leadscrew is. I end up having to run prints with the nuts pretty loose to not get banding from Z wobble. This is an issue with the pom nuts and imperfect screws though, not your adapters.

If you want to give printed nuts a try, here are the F360 files. I have only personally used the 2/2 on my builds.
[T8, 2mm Pitch, 2mm Lead](https://a360.co/2J0gFDd)
[T8, 2mm Pitch, 4mm Lead](https://a360.co/2TucnJ6)
[T8, 2mm Pitch, 8mm Lead](https://a360.co/2TD425n)

The latest nylon nuts honestly feel better on the rods than the POM nuts I used with the adapter. I used a .25mm nozzle and .1 layers so that the internal surface is as close to shape as possible. all extrusion widths set to .26, again for accuracy.

I am going to actually design up some shaft couplers using this same concept, see if I can get rid of the wobble with some intentionally placed compliance.

ChipTechno, 2020-04-19:
@trevjonez thank for the feed back. I will try your design when i get the new small nozzle. How often do you need to replace the printed nut?

trevjonez, 2020-04-19:
6 months or so iirc.

gregsaun, 2020-04-29:
@trevjonez would be nice to have this stored somewhere, like this I can share it in community's optional parts

ChipTechno, 2020-05-27:
I ended up by drill 2 extra holes on the nut using a 3d printed template.
https://photos.app.goo.gl/iB7JpruGCVNLAU9k9

Closed 2021-11-27.

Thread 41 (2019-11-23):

Compatability for linear guideways

nikhil8333, 2019-11-23:
hi, I am trying to make my own design of printer, and tried to accommodate it on the the linear guide-way of hgh15 please help me with, I don't want you to create a X carriage for my use case, but to create a back plate that can be fitted to any X carriage making it universal. hopping you would help me, thanks in advance

gregsaun, 2019-12-16:
Hello, I would love to have time to help you on such a cool project but unfortunately it is not possible anymore today.

I am planning to rework in depth the X axis but we have to finish few ongoing project at the moment (like the Y axis linear rail).

nikhil8333, 2019-12-16:
Well that's sad to hear, but now I am trying with some bull gear model inspiration and will put it on GitHub soon, love to work alongside with you, ping when you get time

gregsaun, 2019-12-17:
What is bull gear model?

Closed 2020-03-10.

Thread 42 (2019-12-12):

Filament sensor is always triggered

Sjoerrdd, 2019-12-12:
Hi,
My filament sensor is always triggered, only if I put it out of the extruder it returns 'OPEN' (M119 command).

gregsaun, 2019-12-12:
May I ask you to share a pic with sensor close and sensor open? This might save some words ;-)

Which printer do you run? MK2.5S or MK3S?

Sjoerrdd, 2019-12-13:
I'm using the MK3S extruder, I'll send a picture when I'm home. (± 5 hours from now)

Sjoerrdd, 2019-12-13:
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

gregsaun, 2019-12-15:
Thank you for your image. I see several issues on your extruder. Could you give me more precision about those points?

- Blue arrow: the carriage is not aligned with extruder body. This could bend the connector and so the sensor PCB making the reading difficult.
- Green arrow: sounds like there is a crack or opening here, make sure not light enters here
- Yellow arrow: not linked to the filament sensor but you are using a pancake stepper which will have not enough torque and loose steps.
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

Sjoerrdd, 2019-12-15:
Thanks,
* That's right, I solved that by printing a new carriage, thanks :)
* It isn't a crack, it's a failed layer (I don't have enough PETG to reprint it), when my new roll arrives, I'll fix it
* Pancake stepper motor is temporarily, the new one will arrive later this week. (the original broke :( )

gregsaun, 2019-12-15:
When no filament is inserted you have the opening here that looks too big. Could you find why?
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

gregsaun, 2019-12-15:
Also could you try the filament sensor out of the body?

Sjoerrdd, 2019-12-15:
It worked, there were some "pustules" on the back of the lever, so it was pushed too far forward.

Thanks for helping :)

gregsaun, 2019-12-15:
Great!

Closed 2019-12-15.

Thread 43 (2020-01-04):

Bondtech Mosquito X-Carriage and X-Carriage Back MK3S

ctilley83, 2020-01-04:
Something to check.  For the lower single bearing, the X Carriage back is not clamping against the bearing.  This results in significant slop. I'm using the Bondtech mosquito X carriage in optional parts, with the x carriage back in the mk3s printed parts in the dev branch.  Maybe I'm mismatching by mistake?

gregsaun, 2020-01-05:
I double checked my files and this is not an issue, it should clamp correctly.

Could you check that the bottom of the X carriage isn't broken and that you are using M3x10mm screws (sometimes people are confusing with M3x12mm screws)?

Closed 2020-03-10.

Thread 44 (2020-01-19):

request x_end_idler scad

CsepregiArtur, 2020-01-19:
Hello

can you please share the x_end_idler scad?

I made an upgrade from an anet A8 but my steel rods are longer, I didn't take that in count that, now I want to test out the printer, but the rods are too long :(.
I would need the scad to modify in that part to be able to fit the longer rods.
this would be only a temporary solution, after that, I want to cut the rods, but still, now I'm not sure its oke all the setup.

gregsaun, 2020-01-23:
I have no SCAD files, everything is designed under Fusion 360. You can find the Fusion 360 source file here with the whole assembly :
https://github.com/gregsaun/bear_extruder_and_x_axis/blob/master/src/bear_extruder_x_axis.f3z

gregsaun, 2020-01-23:
Oops closed too quickly :)

CsepregiArtur, 2020-01-23:
Thank you!!!!!

On Thu, 23 Jan 2020 at 12:30, Grégoire Saunier <notifications@github.com>
wrote:

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

Closed 2020-03-10.

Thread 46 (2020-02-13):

Which material to use?

St0RM53, 2020-02-13:
Regarding printing nozzle_fan_duct i have the following materials:
- Prusament PLA/PETG/ASA
- EasyABS
- CPE HG100
- ColorFabb XT-CF20

Which one you recommend using?

Kind regards

trevjonez, 2020-02-14:
The stock prusa fan nozzle is ASA. I would expect the ASA, ABS, CPE HG100 and XT-CF20 to all perform well for the part. The ABS is likely the most cost effective solution.

gregsaun, 2020-02-14:
Yes I would go ASA probably. I am personally using Extrudr GreenTec Pro but it is expensive (but no styrene and biodegradable). If you never tried annealing HTPLA I would avoid trying that on the shroud, need a bit of experience I think.

St0RM53, 2020-02-15:
Thanks i ended up printing it in ASA successfully :)

Closed 2020-02-15.

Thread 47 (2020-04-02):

Hemera fan knocks on the x-motor-end

knickohr, 2020-04-02:
I build up my new Bear 2.1 with the BEARmera. There is maybe a little problem with the dimensions of some parts. The Hemera fan knocks on the x-motor-end while going left to the startup position. So, until there is no endstop switch (MK3s) the fan drives into the left side. On the second picture you see, there is some space left between the x-motor-end and the x- carriage.

Thomas

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

gregsaun, 2020-04-02:
It is because you are using the old X ends, you need to use the new ones from the dev branch.

knickohr, 2020-04-02:
Really ?  I'm sure I've use the ones from the dev.

knickohr, 2020-04-02:
Ahhh, OK. I see. So I also used the wrong x end idler and the x carriage ?

gregsaun, 2020-04-02:
Not that I see. Sorry, should be easier soon as everything will be available from the github.

knickohr, 2020-04-02:
x carriage back is different too, x carriage and x end idler are OK. Seems I mixed parts. Or I used an earlier dev version ?

gregsaun, 2020-04-02:
No it was available at the same time as the BearMera files. You have to get the X ends, X carriage back and cable guide back from the dev branch.

knickohr, 2020-04-02:
OK, all the parts with date "2 months ago".

gregsaun, 2020-04-02:
This is correct, if you check the X end motor for example you will see that the shape of the arm is different than yours.

knickohr, 2020-04-05:
Fixed ! :-)
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

Closed 2020-04-05.

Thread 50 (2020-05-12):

BOM for scratch build

sfritz67, 2020-05-12:
Hi,
I'm looking to build a bear Prusa from scratch and had a look at the Additional BOM for scratch build for bear_extruder_and_x_axis.

In the BOM, idler is 2GT 20T, but in assembly guide it is 2GT 16. Which is the right part?

By the way, there are some parts from scratch missing from BOM like E3D extruder, bearings, maybe others.

Thank you for your great work.

Fred

gregsaun, 2020-05-12:
Hi, the idler is 2GT 20T but the pulley is 2GT 16T, this might be the confusion.

I'll update the bom, thank you!

sfritz67, 2020-05-12:
If I understand well, idler is bigger than pulley...
Does that mean idler center Z level is different than pulley center Z level to have horizontal belt travel on one side?

gregsaun, 2020-05-12:
Yes, correct. The top portion of the belt, the one attach to the carriage, is flat. The return path is angled but this has no influence.

Closed 2021-11-27.

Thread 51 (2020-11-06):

Filament sensor

syky27, 2020-11-06:
Hi, first of all thanks for the work you have done!

Secondly I would like to ask, if you are planning on releasing new version compatible with Prusa's ball bearing filament sensor...?

Thanks a bunch!

gregsaun, 2020-11-06:
Hi, a new version with the latest filament sensor from Prusa is already available and you can find all the details here:
https://github.com/gregsaun/bear_extruder_and_x_axis/blob/master/README.md

syky27, 2020-11-06:
Hi @gregsaun, for the E3D Hemera? https://github.com/gregsaun/bear_extruder_and_x_axis/blob/master/optional_parts/bear_hemera/README.md

I cannot seem to find it...

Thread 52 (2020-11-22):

10mm Bear-Exxa

evdtempel, 2020-11-22:
Hiya,

First of all: thanks for your amazing work and effort on the Bear-projects! I’ve been using a full Bear MK3S - first with the Bear-extruder and currently with the Bearmera - very happily for a while!

Now, I’ve found my original Prusa to have a score in one of it’s X-rods. So, I’ve got to replace it.. I’m probably going to convert it to the Bear-Exxa in the process, but I’m looking for just that little bit extra for an upgrade.

I really dig the [Caribou 10mm X-axis](https://caribou3d.com/en/upgrade-kits/205-caribo-mk3-10mm-x-axis-upgrade-kit.html) for that little bit extra. But unfortunately, that won't work with a 8mm Z-axis.

Would you consider developing a 10mm Bear-Exxa variation? Ideally making variations to work with both 8mm and 10mm Z-axis, also opening up the door for a full 10mm Bear!

gregsaun, 2025-06-24:
Hello, there is a mod for 10mm Z axis here:
https://guides.bear-lab.com/Wiki/community_optional_parts?revisionid=HEAD#Section_Motion_and_axis_1

Closed 2025-06-24.

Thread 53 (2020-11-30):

Step files for cable guide ?

bipsendk, 2020-11-30:
Are the step files (or maybe fusion 360 files) for the cable guide parts available ?

My strips are a bit wider than the holes, and the easiest thing would be to modify the existing parts by just widening the holes a bit.

gregsaun, 2022-03-21:
You can find them here: https://github.com/gregsaun/bear_extruder_and_x_axis/tree/master/source

Closed 2022-03-21.

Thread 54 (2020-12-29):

Regular BMG supprt

Prutsium, 2020-12-29:
Will you consider to base a version on the BMG extruder with the handle on the left to fit your latest extruder parts?
I prefer the most recent design from you but all mod's are based on the older carriage and part.

gregsaun, 2025-06-24:
Have a look to BearExxa V2: https://github.com/gregsaun/BearExxa-V2

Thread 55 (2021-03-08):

Bearmera filament sensor

LeechNL, 2021-03-08:
On the website I read that a filament sensor for the bearmerra is planned for after the 1.0 release. Is this still the case? I love my filament sensor on the MK3S, and not having it would put me off from buying a Hemera

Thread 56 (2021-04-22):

MK3S+ support?

tfendt, 2021-04-22:
Does the current set of models support the MK3S+? All of my printers (MK3S) are currently using the bear extruder and x-axis. What (if anything) would I need to change if I ordered the '+' upgrade from Prusa?

gregsaun, 2021-04-23:
Yes it is compatible with MK3S+. I will update the documentation soon to add this info.

gregsaun, 2021-04-23:
No changes are need as it is only the SuperPinda that has been added to the extruder.

tfendt, 2021-04-23:
Thanks!

Closed 2021-04-23.

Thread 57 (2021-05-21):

mk8 extruder how to mount mk3s?

easonjim, 2021-05-21:
Dear,
     mk8 extruder how to mount mk3s? BearMera extruder is E3D Hemera mount, can you make it to mk8? thanks.

gregsaun, 2021-05-21:
Hi, it is quite some work to adapt it and support it, I am not planning to do it for now sorry.

easonjim, 2021-05-22:
thanks, i change my idea, switch e3d v6 now.

Closed 2021-05-21.

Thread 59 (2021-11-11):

X-ends with not integrated trapezoidal screw to z-motors

Puebllo, 2021-11-11:
Hi,
I've question, because I'm working on new printer, but instead of using z-motors with integrated trapezoidal screw, I want to use normal nema17 motor with coupler (leftovers from previous projects). I see on images that there's not enough clearence for couplers to fit in "inside" of x-ends (bottom of X-axis will hit couplers as it goes fully down).
Now I'm thinking. May I switch sides of X-ends and rotate them upside down, so the trapezoidal screw will be on the bottom of elements ? Are there any downsides of this solution ? switching sides of logic board and psu are obvious, but is there anything else ?

gregsaun, 2021-11-13:
Hello, I have never tried to install them upside down so I don't really know it that works or not. However, there is this video from Melissa that can help you: https://www.youtube.com/watch?v=N1Hm1EWMIEo

Puebllo, 2021-11-13:
Hey, thank you for response. I saw this video in the past and I couldn't find it. Thanks again. If I will have any question I'll open new issue.

gregsaun, 2021-11-13:
In case of, this video is listed in the optional parts from the community here:
https://guides.bear-lab.com/Wiki/community_optional_parts

Closed 2021-11-13.

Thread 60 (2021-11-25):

Bondtech LGX X-carriage compatibility [MK3S + BEAR 2.1 + LGX+ Mosquito Magnum]

gavan1, 2021-11-25:
Hi @gregsaun I have a quick X carriage question, I'de like to practice caution and confirm compatibility.
The terminology `Bondtech Prusa Upgrade extruder` leaves too much ambiguity and room for confusion, but I will assume Bondtech's LGX extruder is considered a `Bondtech Prusa Upgrade extruder`.

`Note that the Bondtech Prusa Upgrade extruder needs a custom firmware, independently of the X axis used.`

**1.** @BondtechAB could you elaborate on the firmware needed?

I am installing the following:

  1. [Bondtech LGX extruder](https://www.bondtech.se/product/lgx-large-gears-extruder/)
  2. [Mosquito Magnum Hotend](https://www.bondtech.se/product/mosquito-magnum/)
  3. [Bondtech LGX carriage for Mk3S](https://www.bondtech.se/product/lgx-x-carriage-for-mk3s-mosquito/)

https://github.com/gregsaun/bear_extruder_and_x_axis/blob/master/optional_parts/bondtech_x_carriage/printed_parts/bear_bondtech_mosquito_mk3s.zip

The above linked zip file includes.

- bondtech_mosquito_x_carriage_mk3s.stl
- x_carriage_back.stl

**2.** Am I able to to use 3. [Bondtech LGX carriage for MK3S](https://www.bondtech.se/product/lgx-x-carriage-for-mk3s-mosquito/)  with the stl files (x_end_motor  + idler)? Or are those X ends (within that zip file) exclusively limited to the x carriage files in that zip ?

Ultimately I want to use the Brear X ends + Bondtech's LGX X-carriage.

@gerdj is your [LGX Mosquito printhead V1.0](https://github.com/gerdj/LGX_Mosquito?fbclid=IwAR3m96zLb75VcGblMM1kiURWXiHzVWzitPj0kWVgTPky3loHiUmYpY3iEhU) needed instead of Bondtech's LGX X-carriage?

Thank you and can't wait to build the frame!

gavan1, 2021-11-25:
I have confirmed with Bondtech that it's this firmware.

https://www.bondtech.se/downloads/firmware/prusa/FW3100-Build4993-Bondtech-MK3S-16-EINSy10a-LGX-Mosquito.zip

Despite the MK3S board being the Einsy RAMBo (MK3S/+) and not an EINSy10a.

gregsaun, 2021-11-27:
Hi @gavan1, unfortunately my carriage is made for the previous Bondtech extruder and not for the LGX. I am not planning to support the LGX for now but I am working on a geared extruder.

Closed 2025-06-24.

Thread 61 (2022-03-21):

x-axis for original extruder

easonjim, 2022-03-21:
Dear gregsaun,
When I used the parts on the left and right ends of the x-axis of the bear in the original mk3s, I found that the original extruder would jam the bottom belt. Is it incompatible with the original extruder parts?
thanks.

gregsaun, 2022-03-21:
Hello, correct, the original extruder is not compatible with the Bear X axis. I have several improvements on the belt path as well as the addition of the tensioner and all this is breaking the compatibility. You can find more information about compatibility here:
https://github.com/gregsaun/bear_extruder_and_x_axis#compatibility

Closed 2022-03-21.

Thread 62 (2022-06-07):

To much wiggle on the right z axis (can wiggle up and down)

BenHartwich2005, 2022-06-07:
I think that isnt supposed to happen when i try lifting the x axis up on the right hand sigh there a lot of room for wiggle on the left site this issue isnt present i properly tightened the bearing but didnt help. Also the z aixs leadscrew nut is properly tightened
Any suggestions?

Closed 2022-06-07.

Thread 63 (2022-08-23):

original extruder body r6 version loose

easonjim, 2022-08-23:
Dear gregsaun,
    I’m printing the original extruder body r6 version and found that the printed circular radiator has a small bayonet, which causes the e3d v6 circular radiator to be too loose. I have calibrated the extruder and there is no problem with the line width. May I ask this question How to solve it?

gregsaun, 2022-08-23:
Hello @easonjim,

The hotend should be loose when it sits only in the extruder body but when you close the extruder cover it shouldn't move anymore. After the step [16](https://guides.bear-lab.com/Guide/3.+Extruder/36?lang=en#s390) the hotend should move a little but after step [17](https://guides.bear-lab.com/Guide/3.+Extruder/36?lang=en#s391) it should be tight.

easonjim, 2022-08-23:
Yes, but I printed the original R6 print model and found that the effect is loose, which is very abnormal;
May I ask what printing needs the society?

gregsaun, 2022-08-23:
Could you please share me a picture of your extruder and the bayonet you have printed?

gregsaun, 2022-08-23:
I see you have opened the [issue on Prusa's Github](https://github.com/prusa3d/Original-Prusa-i3/issues/184). I am not developer at Prusa nor working for them, I just make compatible parts with some improvements. I will close this request as it seems an issue with the Prusa extruder and not my work.

easonjim, 2022-08-23:
Ok, thank you very much gregsaun, I will go to the official and wait for the latest feedback.

gregsaun, 2022-08-23:
Try to contact the Prusa support, it might be faster to get an answer :)

Closed 2022-08-23.

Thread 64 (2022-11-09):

Two different Versions for the x_carriage.stl / bondtech_e3d_x_carriage_mk3s.stl

juckendesAuge, 2022-11-09:
Hello,
I would like to convert X-axis and extruder to Bearmod on my Prusa MK3S+.
Does it work with the + version of MK3S?
Now I am unsure which file to take from the two. Both files are added on 2020-05-11. So unfortunately I can't see which file is newer either.
They are also visibly a little different. In x-carrige.stl, for example, you can still see two hex nut cutouts inside.
The bondtech_e3d_x_carriage_mk3s.stl has 4 holes with recesses for the head, but no recess for hex nuts. The shape also varies a bit.

https://raw.githubusercontent.com/gregsaun/bear_extruder_and_x_axis/master/optional_parts/bondtech_x_carriage/printed_parts/bear_bondtech_e3d_mk3s.zip

bondtech_e3d_x_carriage_mk3s.stl

sha256sum bondtech_e3d_x_carriage_mk3s.stl
853fde48b2968c2cbe761dc8a83abadeb01165c71c8c14138ffb7bb69d4f5f1e bondtech_e3d_x_carriage_mk3s.stl

726K 11. May 2020 bondtech_e3d_x_carriage_mk3s.stl

---

https://raw.githubusercontent.com/gregsaun/bear_extruder_and_x_axis/master/printed_parts/bear_extruder_x_axis_mk3s.zip
x_carriage.stl

sha256sum x_carriage.stl
c4418dcf2ee585574a1f5a4555060b7123b435004d2fb96999e997212a4203c1 x_carriage.stl

701K 11. May 2020 x_carriage.stl

Thank you very much for the help.

Translated with www.DeepL.com/Translator (free version)

gregsaun, 2022-11-09:
Hello @juckendesAuge,

Yes it is compatible with the "+" version :)

The carriage depends which extruder you want to build. The standard Bear extruder that you have to fully print yourself then you will find all information here:
https://guides.bear-lab.com/c/95jghwzvw9l46s3g

It is possible you have the Bondtech extrude which looks like this:
https://www.bondtech.se/product/prusa-i3-mk3s-extruder-upgrade/
In that case it is using a different carriage and you have all information here:
https://guides.bear-lab.com/c/rmf45dv3tqb5uf69

I hope this was helpful :)

juckendesAuge, 2022-11-09:
Hello @gregsaun,

thank you very much for the quick reply. :)

I'm building it with the standard V6 hotend.
I'm concerned with no more scratches in the smooth X-axis rods and easier belt tensioning.

gregsaun, 2022-11-09:
All good with the V6, trusty hotend!

For the scratches make sure to always keep the rods with some grease and clean the dust on the ends regularly. Put some grease inside the bearings before installing them. Another good trick is to print both x_end_idler and x_end_motor together, like if there is a slight variation during the print it will be replicated on both and make them equal.

Enjoy the build :)

juckendesAuge, 2022-11-09:
I clean all Misumi bearings with 99% isopropanol in a glass. After drying, I press lithium-based grease into the bearings.
The Misumi bearings of the X and Y axis I replaced completely with new ones. The four bearings of the Z axis I wanted to clean, grease and continue to use.

Unfortunately I have already printed both x_end_idler and x_end_motor separately, because pet-g pulls otherwise something strings.

gregsaun, 2022-11-09:
Don't leave the bearing too long in IPA as they could rust (balls inside are not stainless steel).

For stringing, if your filament is from good quality and dry you can try to reduce the temperature a little and try to increase retraction speed to 50mm/s. I don't know your wohle setup so take this with a pinch and salt ;)

juckendesAuge, 2022-11-09:
Ok.
Thank you.
Standard MK3s+ with Prusament PET-G.

Should I print the two parts together again, or test first to see if it works with the two I printed separately?

Thank you very much.

gregsaun, 2022-11-09:
If the both prints look good it is not necessary to reprint them 👍

juckendesAuge, 2022-11-10:
Thank you very much. :)

The parts look very good.

The camera can not capture it so well.

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

juckendesAuge, 2022-11-10:
@gregsaun

https://guides.bear-lab.com/Wiki/Bear_FAQ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

Quote:
Firstly, you can flash temporarily an older MK3 firmware, such as 3.7.1, and perform the XYZ calibration. Once calibration is passed, flash the MK3S firmware of your choice to access the full functionality of the MK3S.

Does the Bear Extruder work with the latest firmwae from Prusa (firmware 3.11.0)?
Unfortunately I can not flash the 3.7.1, because the Super Pinda is supported only from firmware version 3.9.2.

Thanks a lot

gregsaun, 2022-11-11:
It does but not for the calibration, just use our Bear firmware as recommended.

juckendesAuge, 2022-11-12:
ok.
Thank you very much.
This is also the penultimate firmware version that was modified. Then it is ok.
I use the Experimental feature:
E-cool mode
https://help.prusa3d.com/article/experimental-menu-mk3-s-_161213

I would like to continue using it.

Many greetings

juck.

Closed 2025-06-24.

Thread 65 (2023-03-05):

firmware update

easonjim, 2023-03-05:
Dear gregsaun,
   I found that the bear's firmware has not been updated for a long time, and the current official firmware has reached 3.12.

vertigo235, 2023-03-05:
The bear firmware is only intended to be used for the calibration steps so you can ensure you have your printer assembled properly.  After that you can upgrade to whatever the latest Prusa FW is and use with no issues.

Closed 2025-06-24.

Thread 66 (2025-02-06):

BTT EBB36 tool head adaption <MOD OFFERING>

Bazmundi, 2025-02-06:
I got a little bogged down trying to sort out wiring up my Bear.  I was building from scratch, so had a bit of a side adventure with bits and bobs.

Eventually I got it to the point of wiring up.   Having sorted out a BTT SKR MINI and a raspberry pi zero 2W with octoprint+klipper.

I poured over various cable management "strategies" (hacks), didn't like any of them.  Then, because I'm plodding and not commited, I late to the party came across "tool heads".

As I had opted to get a Hermera extruder (on the basis there was a Hermera version of the x-axis), [I hope this option helps](https://www.thingiverse.com/thing:6937086).  It's a mod (hack) to allow attachment of a BTT EBB36 tool head widget.

It's the least I can do to support this fantastic work by @gregsaun.

gregsaun, 2025-06-24:
Sorry for the late answer. Thank you very much. I have added it in the list here:
https://guides.bear-lab.com/Wiki/community_optional_parts?revisionid=HEAD#Section_Electronic

Could you please add STEP files and native CAD files?

Thank you in advance

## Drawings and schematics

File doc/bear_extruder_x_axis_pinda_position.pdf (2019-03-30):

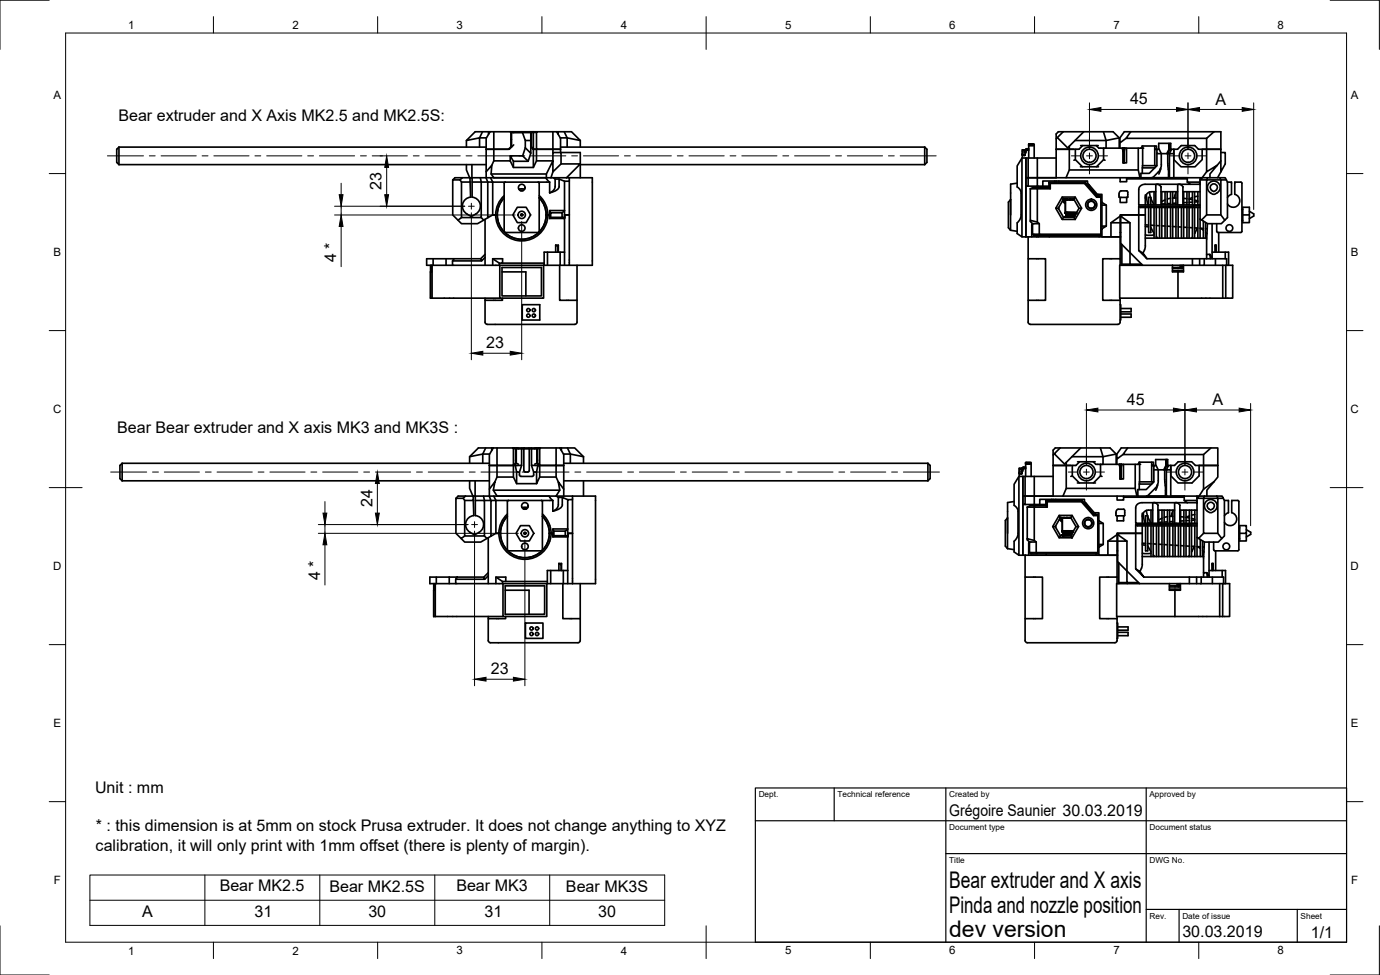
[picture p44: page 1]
Grégoire Saunier 23; Unit : mm

Bear extruder and X Axis MK2.5 and MK2.5S:

Bear Bear extruder and X axis MK3 and MK3S : 24 4 *

Dept. | Technical reference | Created by 30.03.2019 | Approved by

* : this dimension is at 5mm on stock Prusa extruder. It does not change anything to XYZ
calibration, it will only print with 1mm offset (there is plenty of margin).

Document type | Document status

Title Bear extruder and X axis Pinda and nozzle position dev version | DWG No.

Bear MK2.5 | Bear MK2.5S | Bear MK3 | Bear MK3S

Rev. | Date of issue 30.03.2019 | Sheet 1/1

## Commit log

2018-05-01 extruder idler use only one screw. motor is again 1mm closer to rods. better fit for filament sensor connector
    [extruder_idler.stl, filament_sensor_cover.stl, x_carriage.stl]
2018-05-03 improved hotend cooling opening, filament sensor holes, nozzle fan arm, all cables guides, hotend opening, centering hole for motor
    [cable_guide_back_a.stl, cable_guide_back_b.stl, extruder_body.stl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]
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2018-05-06 fix position issue of filament sensor
    [x_carriage.stl]
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2018-05-15 improve motor centering, remove filament sensor cleaning hole
    [extruder_body.stl]
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2018-05-16 stronger intake for hotend cooling and closer to noctua shape
    [extruder_body.stl]
2018-05-25 improve top holes, center square nut pocket and clip of filament sensor connector
    [x_carriage.stl]
2018-05-26 fix print orientation and make parts 1mm thicker
    [cable_guide_back_a.stl, cable_guide_back_b.stl]
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2018-05-27 improve selective infill, increase bearing outside dia, improve bearing alignement in x-end idler mount
    [x_end_idler.stl, x_end_idler_idler_mount.stl, x_end_motor.stl]
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2018-05-31 improve printing quality. improve selective infill. stronger bearing holder. improve bearing mount in idler
    [x_end_idler.stl, x_end_idler_idler_mount.stl, x_end_motor.stl]
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2018-08-07 fix wrong screw length for optional rods tensioner
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2018-08-08 tighter smooth rods and Z bearings holes
    [x_end_idler.stl, x_end_motor.stl]
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2018-08-23 add reverse bowden
    [filament_sensort_pc4-m10.stl, filament_sensort_pc4-m5.stl, filament_sensort_pc4-m6.stl]
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2018-08-23 20T X axis idler and add clamps for Z bearings on X ends
    [x_carriage.stl, x_end_idler.stl, x_end_idler_idler_mount.stl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]
2018-08-23 not useful anymore due to clamps on X ends
    [z_bearings_installer.stl]
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2018-08-29 add a better jointure between cover and body on the hotend fan side to prevent not perfectly closed body to leak air on the heatblock. Reduce self threading holes diameter
2018-08-30 improve jointure between cover and body. reduce self threading holes. Fix chamfer on bottom of extruder body
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2018-09-04 improve belt path by taking bearing dia tolerance into account. Improve belt teeth shape to get closer to Gates GT2/3 specs
2018-09-04 fix pinda position issue. fix manifold issue. fix bridging issue while printing the pinda mount. add chamfers to remove elephant foot issue
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2018-09-06 improve belt position tolerance and selective infill
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2018-09-20 fix hole depth error. improve belt path and square nut pocket
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2018-09-20 add vslot mount for reverse bowden
    [vslot_mount_pc4-m10.f3d, vslot_mount_pc4-m10.stl, vslot_mount_pc4-m10_angled.f3d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]
2018-09-21 use M3x10 screw to adjust smooth rod tension
    [x_end_idler.stl, x_end_idler_idler_mount.stl]
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2018-09-21 PETG only, PLA might broke on the vslot mount and filament sensor cover might melt due to the motor temp
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2018-09-23 wrong place for extruder idler bearing stl
    [extruder_idler_bearing.stl]
2018-09-23 reduce screw hole dia to get a better jointure between two parts
    [cable_guide_back_a.stl, cable_guide_back_b.stl]
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2018-09-23 improve cable guide and avoid the cables to have a chance to be pinched
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2018-10-22 This fixes #17. Reduce PTFE hole by 0.05mm for better fitting
2018-10-22 This fixes #18. Makes more room for idler pulley in case the X axis is not perfectly square
    [x_end_idler.stl, x_end_idler_idler_mount.stl]
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2018-10-22 X motor closer to pulley to reduce torque on motor shaft
    [x_end_motor.stl]
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2018-10-25 fix position on the bed
2018-10-27 fix wrong teeth profile for idler
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2018-10-28 increase bearing idler mount width to better support not perfect assemblies
    [x_end_idler.stl, x_end_idler_idler_mount.stl]
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2018-11-09 improve filament sensor pocket spacing and add light leak protection. slight tuning on hotend cooling
    [filament_sensor_cover.stl, filament_sensor_cover_pc4-m10.stl, x_carriage.stl]
2018-11-09 fix wrong belt reference
2018-11-09 fix wrong idler tooth profile
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2018-11-11 improve holes for motor and laser sensor cover. improve light leak protection
    [filament_sensor_cover.stl, filament_sensor_cover_pc4-m10.stl]
2018-11-11 add compatibility with drop in t-nuts. longer arm. adjust clearance for PC4-M10 hole
    [vslot_mount_pc4-m10.stl, vslot_mount_pc4-m10_angled.stl]
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2018-11-13 fix selective infill and POM mount obstruction
    [x_end_idler.stl]
2018-11-13 make motor mount stronger and fix selective infill
    [x_end_motor.stl]
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2018-11-15 bigger chamfer for better fit. improve pocket nut on idler mount
    [x_end_idler.stl, x_end_idler_idler_mount.stl]
2018-11-16 fix weak belt clamp
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2018-11-17 rework belt clamp
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2018-11-18 improve clearance for extruder cover jointure
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2018-11-19 replace bondtech shaft by dowel pin
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2018-11-19 add 0.1mm on idler mount to better accomodate longer dowel pin
    [x_end_idler.stl, x_end_idler_idler_mount.stl]
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2018-12-28 Add missing E motor, belt and smooth rods
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2019-01-05 fix filament sensor source opening issue
    [filament_sensor_cover_pc4-m10.f3d, filament_sensor_cover_pc4-m10.f3z]
2019-01-06 Add printed part shortcut and description
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2019-01-11 Add missing parts for the back of the carriage
2019-01-14 fix nozzle fan dimensions
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2019-01-16 Fix head position, set bed temp
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2019-02-07 fix bom quantity
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2019-03-02 redo MK3 carriage with derive method from Fusion 360
    [x_carriage.stl]
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2019-03-03 fix selective infill
    [x_carriage.stl]
2019-03-03 fix dimension for IR sensor opening
    [x_carriage.stl]
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2019-03-03 fix ball opening
    [filament_sensor_lever.stl]
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2019-03-16 add filament sensor cover for reverse bowden on MK2.5S and MK3S
    [fs_cover_pc4-m10_mk25_mk3.step, fs_cover_pc4-m10_mk25_mk3.stl, fs_cover_pc4-m10_mk25s_mk3s.stl]
2019-03-16 add step for fs cover reverse bowden MK2.5S MK3S
    [filament_sensor_cover_pc4-m10.step, filament_sensor_cover_pc4-m10.stl, fs_cover_pc4-m10_mk25s_mk3s.step]
2019-03-16 make the walls closer to hotend to improve cooling
    [extruder_cover.stl]
2019-03-16 improve hotend cooling, new pinda mount to better resists to heat, use shorter 45mm PTFE like MK2.5S and MK3S, improve tolerances on filament sensor
    [filament_sensor_cover.stl, filament_sensor_lever.stl]
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2019-03-17 fix filament guide issue around bondtech gears. Make hotend assembly easier
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2019-03-23 Smaller extruder body. Easier hotend assembly. Improved alignment tab for extruder cover. Improve printing of pinda mount
    [extruder_cover.stl, filament_sensor_cover.stl, fs_cover_pc4-m10_mk25s_mk3s.stl]
2019-03-23 carriage rework to support new filament sensor cable
    [x_carriage.stl, x_carriage_back.stl]
2019-03-23 remove MK2.5 and MK3 to support only MK2.5s and MK3s
    [filament_sensor_cover.stl, filament_sensor_cover_pc4-m10.f3z, filament_sensor_lever.stl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]
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2019-03-28 fix an issue with the mounting screw that could squish the zip ties holes
    [cable_guide_back_a.stl, cable_guide_back_b.stl]
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2019-04-04 add different shroud design with large lateral cooling
    [nozzle_fan_duct_lateral.stl]
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2019-04-06 update bondtech X carriage to latest Bear extruder version
    [bondtech_x_carriage_mk3.f3z, bondtech_x_carriage_mk3.stl]
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2019-04-10 reassemble some test and create bridge and short layer tests for nozzle shroud
    [bear_bridge_35-50-65.f3d, bear_bridge_35-50-65.stl, bear_full_surface_bed.f3d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]
2019-04-12 reduce bottom surface. smoother intake. reinforced mount
    [nozzle_fan_duct.f3d, nozzle_fan_duct.stl]
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2019-04-16 smoother insertion of filament with reverse bowden
    [filament_sensor_lever.stl]
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2019-04-22 remove the source, now include in extruder assembly source file
    [nozzle_fan_duct.f3d]
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2019-04-29 fix bearing diameter
    [x_end_idler.stl, x_end_idler_idler_mount.stl, x_end_motor.stl]
2019-04-30 add chamfer to ensure not PTFE can get stock in bad position during insertion
    [extruder_body.stl]
2019-05-01 increase again by 0.3mm the Z bearing hole
    [x_end_idler.stl, x_end_idler_idler_mount.stl, x_end_motor.stl]
2019-05-03 make hotend insertion easier and less prone to errors
    [extruder_body.stl]
2019-05-08 add 2 more angles and reduce difference between length of layers
    [bear_moire.stl]
2019-05-08 add optional X carriage back for larger cables and cables from laser sensor for the Bondtech extruder
    [x_carriage_back_mk2.5_laser.stl, x_carriage_back_mk3_laser.stl]
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2019-05-08 fix scale bug from F360
    [bear_moire.stl]
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2019-05-12 rollback to 50mm PTFE tube and 1mm higher body like 0.6.0
    [bondtech_x_carriage_mk2s_mk2.5_mk2.5s.f3z, bondtech_x_carriage_mk2s_mk2.5_mk2.5s.stl, bondtech_x_carriage_mk3_mk3s.f3z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]
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2019-05-12 cable guide screw goes a little deeper again
    [cable_guide_back_a.stl, cable_guide_back_b.stl]
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2019-05-21 add optional part to use E3D toothed idler
    [e3d_idler_mount.f3z, x_end_idler_tensioner_e3d.stl]
2019-05-23 raise blower to for smoother shroud internals. nicer shroud print
    [extruder_cover.stl, nozzle_fan_duct.stl]
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2019-05-27 fix hold togheter bottom screw that might be too close to e3d v6
    [bondtech_x_carriage_mk2s_mk2.5_mk2.5s.f3z, bondtech_x_carriage_mk2s_mk2.5_mk2.5s.stl, bondtech_x_carriage_mk3_mk3s.f3z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]
2019-05-27 switch lead screw nut hole diameter to same as Prusa o make centering easier
    [x_end_idler.stl, x_end_idler_tensioner.stl, x_end_motor.stl]
2019-05-28 improve airflow around the bottom hold togheter screw
    [extruder_body.stl]
2019-05-30 fix print orientation
    [x_end_idler.stl, x_end_idler_tensioner.stl]
2019-05-30 improve X axis bearing tightening
    [bondtech_x_carriage_mk2s_mk2.5_mk2.5s.f3z, bondtech_x_carriage_mk2s_mk2.5_mk2.5s.stl, bondtech_x_carriage_mk3_mk3s.f3z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]
2019-05-30 make heatsink opening stronger to better resist to torque when screwing the heatsink fan
    [extruder_body.stl]
2019-06-03 stronger filament sensor and easier to print. improve filament path before gears. stronger and deeper hotend fan screw holes
    [extruder_body.stl, extruder_cover.stl, filament_sensor_cover.stl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]
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2019-06-03 reinforce bottom hotend fan hole. smoother grid outlet
    [extruder_body.stl]
2019-06-04 fix too fragile hotend fan screw hole. fix filament sensor components hitting pocket. increase angled bridge on the pinda mount
    [extruder_body.stl]
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2019-06-07 more margin for Z tops of stock frame
    [x_carriage_back.stl, x_carriage_back_mk2.5_larger_cable.f3z, x_carriage_back_mk2.5_larger_cable.stl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]
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2019-06-10 fix link to stl
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2019-07-15 Add Bondtech MK2.5S and MK3S Bear X carriage
    [bondtech_x_carriage_mk2.5s.f3z, bondtech_x_carriage_mk2.5s.step, bondtech_x_carriage_mk2.5s.stl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]
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2019-09-08 fix bom link
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2020-02-05 increased space for hemera, stiffer and faster to print, add self centering kinematic.
    [x_end_idler.stl, x_end_idler_tensioner.stl, x_end_motor.stl]
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2020-02-05 more room for cables. stiffer and more durable cable guide arm. rework selective infill
    [bondtech_mosquito_x_carriage_mk2.5s.f3z, bondtech_mosquito_x_carriage_mk2.5s.step, bondtech_mosquito_x_carriage_mk2.5s.stl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]
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2020-03-10 quicker to print. add print settings. add more angles
    [bear_overhang_45-75.f3d, bear_overhang_45-75.stl, bear_overhang_50-70.f3d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]
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2020-04-02 Remove wrong detail for M3x14mm screw
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2020-04-17 tighter pinda holding, reduce selective infill, reduce v6 tolerance, tighter square nut on back, improve print quality for mid air holes, nicer fitting with latest X carriage back
    [extruder_body.stl]
2020-04-17 reduce v6 tolerance, improve selective infill, improve print quality
    [extruder_cover.stl]
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2020-04-29 Add leadscrew nuts to community listing
    As mentioned in https://github.com/gregsaun/bear_extruder_and_x_axis/issues/40#issuecomment-621237666
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2020-05-02 add Nylon filament guide for extruder. Fix raw links
2020-05-02 fix link and regenarte PDF for bom
2020-05-04 fix direct link
    [body_front_volcano.stl]
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2020-05-04 fix links. Print settings improved
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2020-05-26 fix bondtech gears link
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2020-08-01 fix E3D store link for idler
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2025-04-19 fix 2GT 16T pulley desc
